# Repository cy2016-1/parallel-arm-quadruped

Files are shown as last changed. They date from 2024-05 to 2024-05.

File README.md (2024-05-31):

# 并联臂四足

#### 硬件设计
    单片机：STM32F103C8T6
    电源方案：7.4V-12V输入，通过XL4005E1输出5V给舵机供电，再通过RT9013输出3.3V给单片机供电
    通信：NRF24L01
    舵机驱动：方案一：直接通过2个定时器产生8路PWM输出；方案二：通过IIC与PCA9685通信，驱动舵机
#### 软件架构
1.产生摆线方程，生成足端轨迹规划
    sigma=2pi(t-t_T)/(faaiTs);
    Xep=((xf-xs)(sigma-(sin(sigma))))/(2pi)+xs;
    Zep=h(1-cos(sigma))/2;

2.运动学逆解（余弦定理、勾股定理）
输入图片说明 屏幕截图
A、B分别为两个舵机输出轴心，它们相距距离为2a。足端坐标（x,y）由轨迹规划而来。L1，L2为腿部的上臂和下臂臂长。
θ1和θ2才是我们需要求解的舵机转动角度。
而θ1=90°-（β-γ），所以求解顺序为：L3→β→γ

3.用MPU6050传感器反馈数据来实现姿态控制
输入图片说明 屏幕截图

#### 注意事项

1.  组装舵机前，先下载舵机回中位的程序，即将 main.c中的这部分注释掉，如图
输入图片说明 屏幕截图
2.  注意舵机引脚分配：FR-前→A6，FR-后→A7;BR-前→B0,BR-后→B1;BL-前→B8,BL-后→B9;FL-前→B6,FL-后→B7

#### 展示
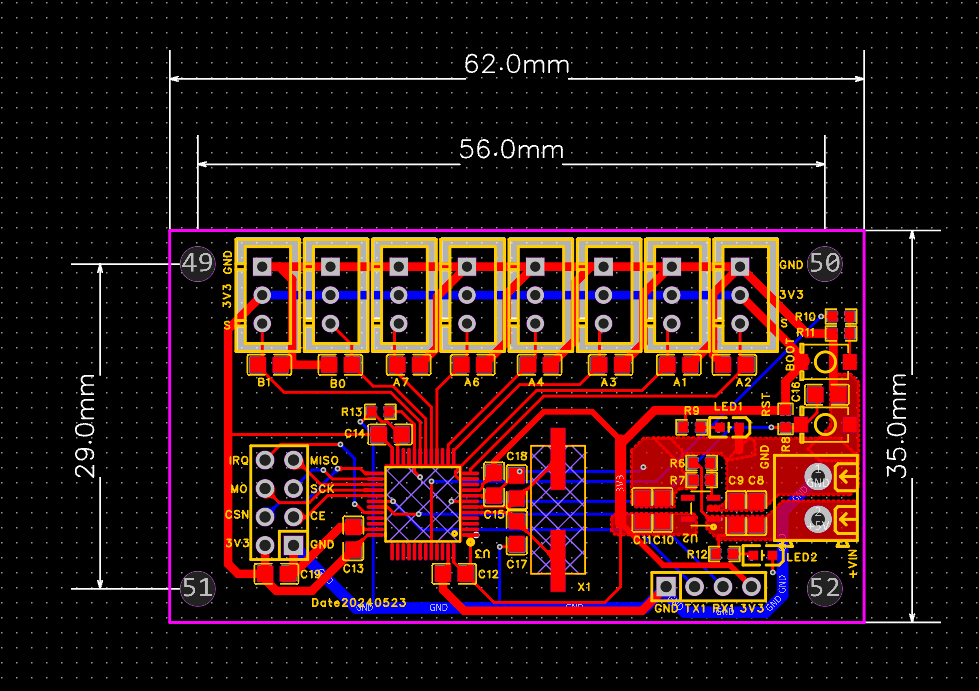
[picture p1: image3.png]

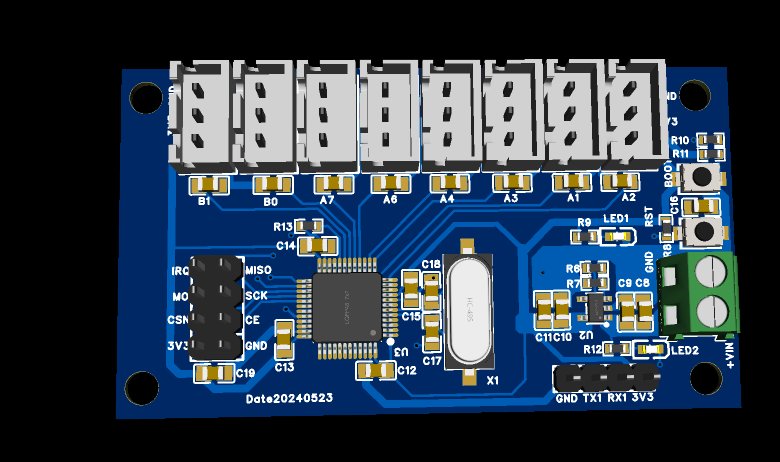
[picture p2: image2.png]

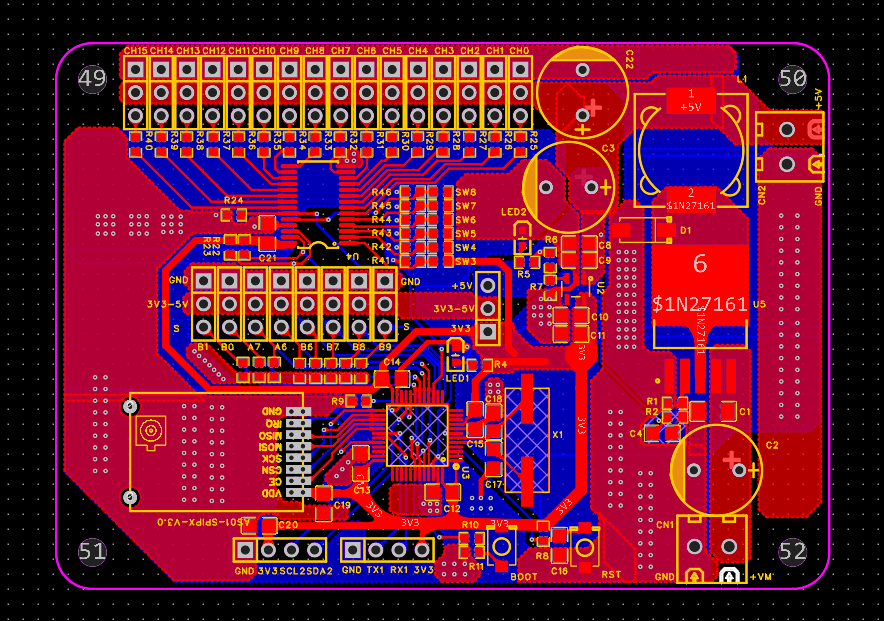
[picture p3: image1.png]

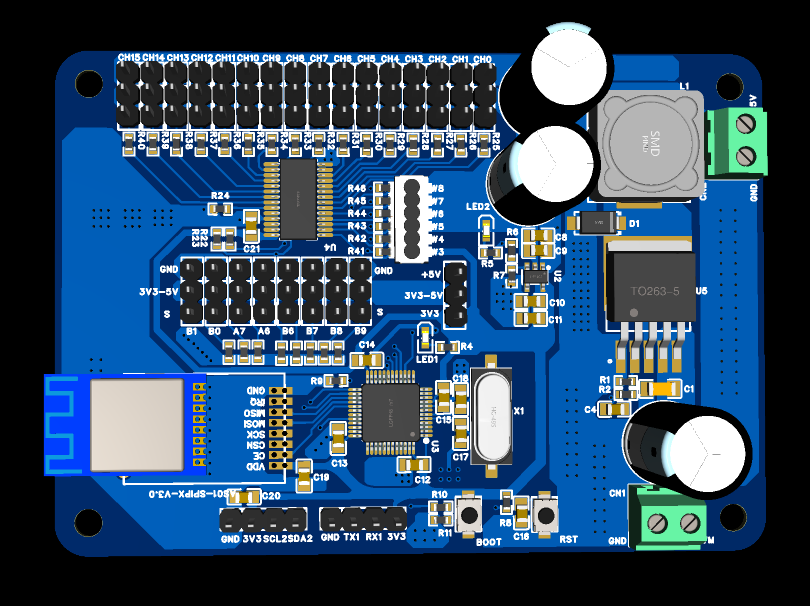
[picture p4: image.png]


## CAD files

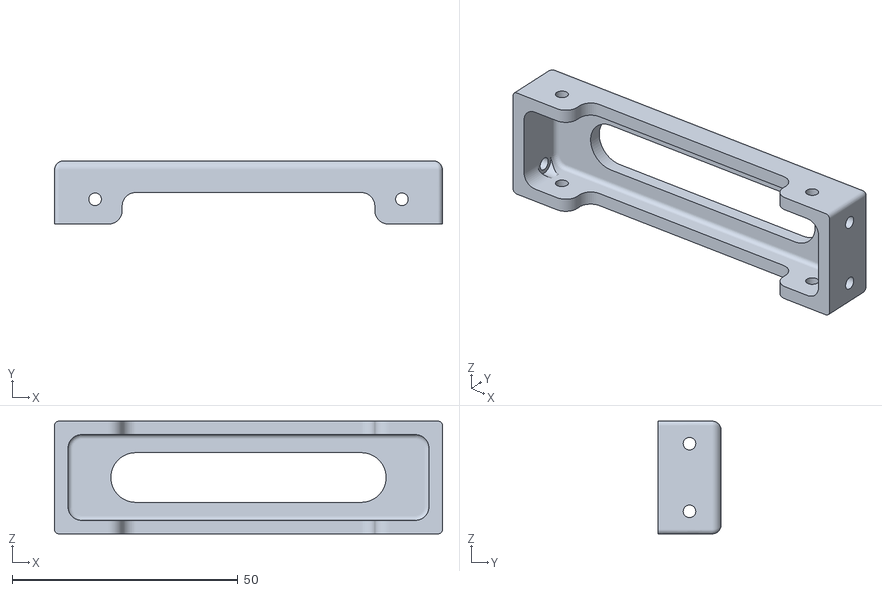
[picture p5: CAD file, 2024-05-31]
STL文件/前后横板.stl
86.0 x 14.0 x 25.0

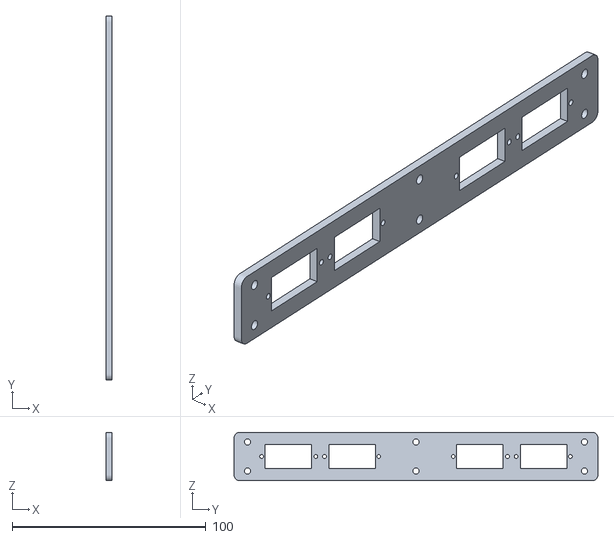
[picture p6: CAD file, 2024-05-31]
STL文件/舵机固定板.stl
3.00 x 188.0 x 25.0

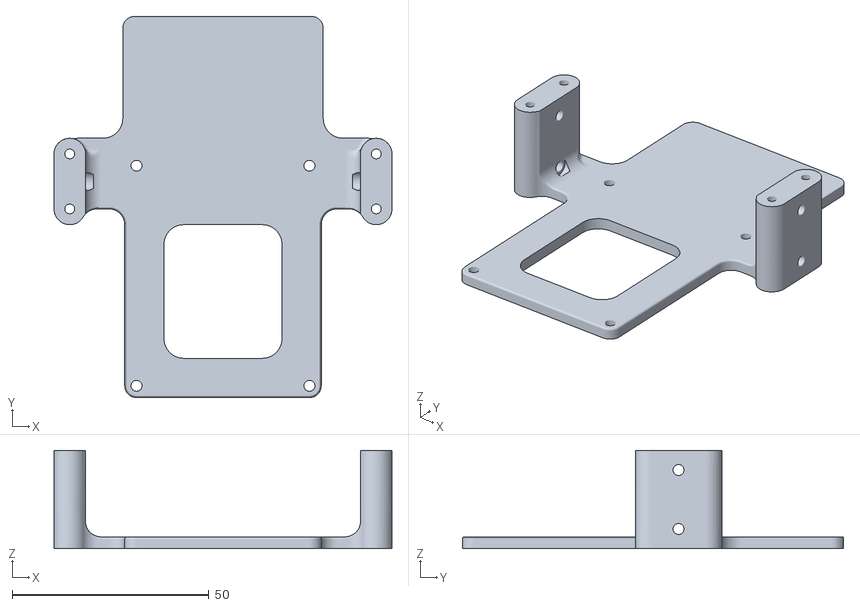
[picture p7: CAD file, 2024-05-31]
STL文件/中间横板.stl
86.0 x 97.0 x 25.0

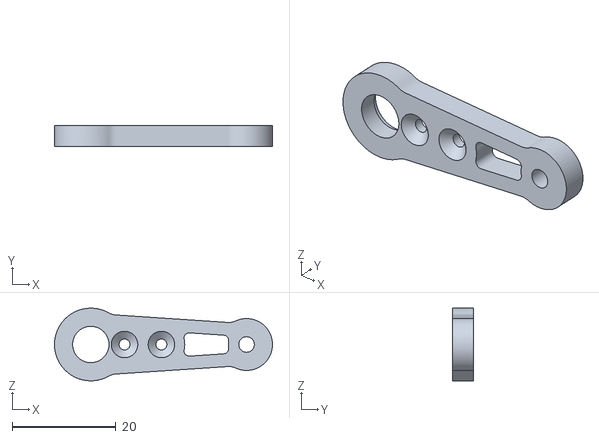
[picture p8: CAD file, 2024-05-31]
STL文件/大臂.stl
42.0 x 4.00 x 14.0

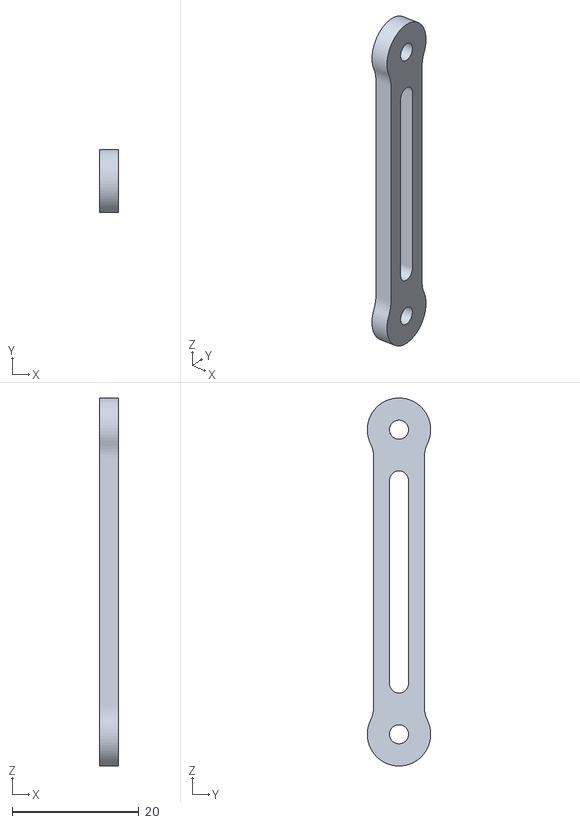
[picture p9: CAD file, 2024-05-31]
STL文件/下臂后.stl
3.00 x 9.99 x 58.0

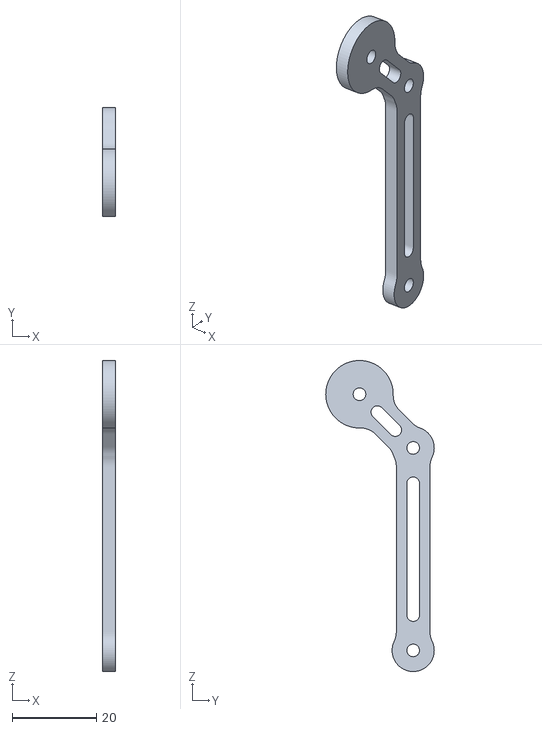
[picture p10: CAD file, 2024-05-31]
STL文件/下臂前.stl
3.00 x 25.7 x 73.7

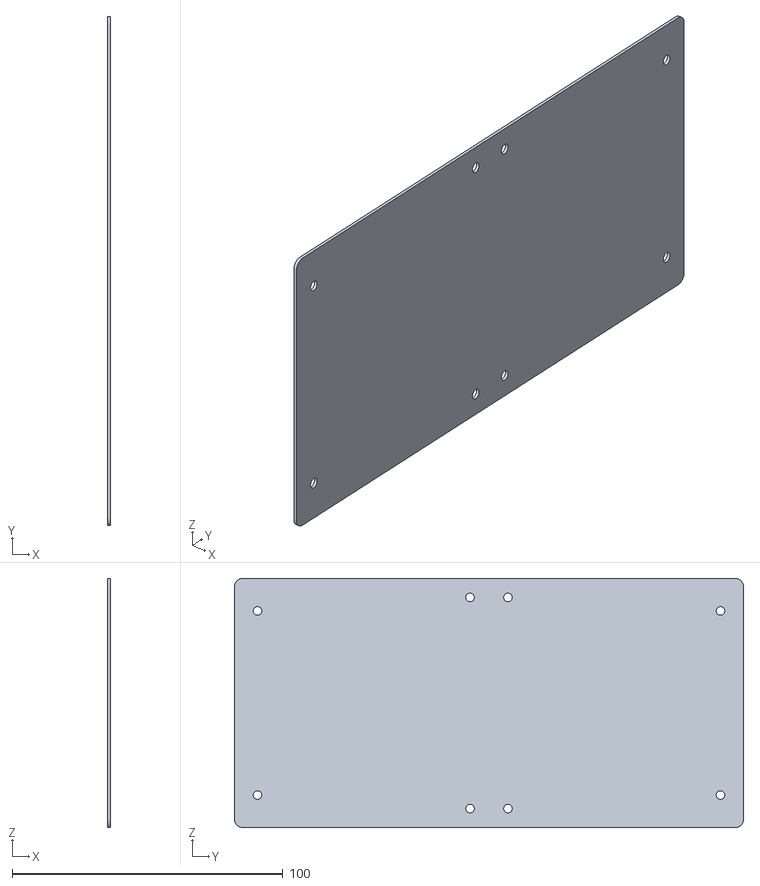
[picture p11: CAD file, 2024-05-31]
STL文件/机身上下盖板.stl
1.00 x 188.0 x 92.0

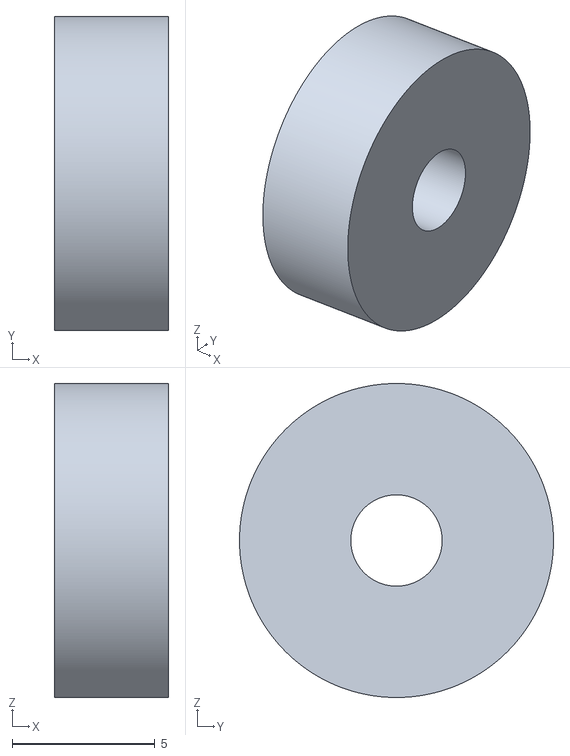
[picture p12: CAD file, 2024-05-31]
STL文件/圆垫3mm.stl
4.00 x 11.0 x 11.0

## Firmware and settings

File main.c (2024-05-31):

#include "./SYSTEM/sys/sys.h"
#include "./SYSTEM/usart/usart.h"
#include "./SYSTEM/delay/delay.h"
#include "./BSP/TIMER/gtim.h"

#include "./BSP/NRF24L01/nrf24L01.h"
  
#include "./BSP/KEY/key.h"
#include "demo.h"
//#include "./BSP/PCA9685/pca9685.h"
//#include "./BSP/IIC/myiic.h"

#include <math.h>

extern TIM_HandleTypeDef g_tim3_pwm_ch_handle;     /* 定时器3ch3句柄     PB0     */
extern TIM_HandleTypeDef g_tim2_pwm_ch_handle;     /* 定时器3ch3句柄     PB0     */
extern TIM_HandleTypeDef g_tim4_pwm_ch_handle;     /* 定时器3ch3句柄     PB0     */

extern float imu_buf[10];
extern float walk_xy[8],t_speed;
extern int Motion_state;
int16_t map(float val,int16_t map_I_min,int16_t map_I_max,int16_t map_O_min,int16_t map_O_max)
{
	int16_t map_val=(int16_t)(val);
  if(map_val<map_I_min)
    {
      return map_O_min;
    }
  if(map_val>map_I_max)
    {
      return map_O_max; 	
    }
//		return  (map_val*(map_O_max-map_O_min)/(map_I_max-map_I_min))+(map_O_max-map_O_min)/2;
  return  (map_val*10/9)+150;
}
float L1=30,L2=48,L3=62.0474,DIS_X=21/2;	
float P_x=0,P_y=60,P_z=60;					


float Xs=0,Xf=10,H=10,PI=3.14,delta_X=0;//Xf=-20

float x1,x2,x3,x4,y1,y2,y3,y4;
extern float pi;
float ABl_x,ABl_z,AB2_x,AB2_z,AB3_x,AB3_z,AB4_x,AB4_z;
float pwm_out[4][4]={{0,150,0,150},{0,150,0,150},{0,150,0,150},{0,150,0,150}};
void IK_calculate(float IK_x,float IK_y,int IK_i){
	float IK_angle1,IK_angle2,IK_angle3,IK_angle4,IK_angle5,IK_x_1,IK_y_1,IK_angle6,IK_angle7,IK_angle8,IK_angle9=0.3336;
	if((IK_x-DIS_X)==0){
		IK_angle1=0;
	}else{
		IK_angle1=asin((IK_x-DIS_X)/(sqrt((IK_x-DIS_X)*(IK_x-DIS_X)+IK_y*IK_y)));
	}
	IK_angle2=acos(((IK_x-DIS_X)*(IK_x-DIS_X)+IK_y*IK_y+L1*L1-L3*L3)/(2*L1*sqrt((IK_x-DIS_X)*(IK_x-DIS_X)+IK_y*IK_y)));
	IK_angle3=1.57-IK_angle2-IK_angle1;
	pwm_out[IK_i][2]=-IK_angle3;
	pwm_out[IK_i][3]=map(-IK_angle3*57.3,-90,90,50,250);
	IK_angle4=acos((L1*L1+L3*L3-((IK_x-DIS_X)*(IK_x-DIS_X)+IK_y*IK_y))/(2*L1*L3));
	IK_angle5=IK_angle4-IK_angle3-IK_angle9;
	IK_x_1=L1*cos(IK_angle3)-L2*cos(IK_angle5)+DIS_X*2;
	IK_y_1=L1*sin(IK_angle3)+L2*sin(IK_angle5);
	
	if(IK_x_1==0){
		IK_angle6=0;
	}else{
		IK_angle6=asin(IK_x_1/(sqrt(IK_x_1*IK_x_1+IK_y_1*IK_y_1)));
	}
	IK_angle7=acos((IK_x_1*IK_x_1+IK_y_1*IK_y_1+L1*L1-L2*L2)/(2*L1*sqrt(IK_x_1*IK_x_1+IK_y_1*IK_y_1)));
	IK_angle8=1.57-IK_angle7+IK_angle6;
	pwm_out[IK_i][0]=IK_angle8;
	pwm_out[IK_i][1]=map(IK_angle8*57.3,-90,90,50,250);
}

void PWM_OUT(){
	__HAL_TIM_SET_COMPARE(&g_tim3_pwm_ch_handle, GTIM_TIM3_PWM_CH1, 300-pwm_out[0][1]);
	__HAL_TIM_SET_COMPARE(&g_tim3_pwm_ch_handle, GTIM_TIM3_PWM_CH2, 300-pwm_out[0][3]);

	__HAL_TIM_SET_COMPARE(&g_tim3_pwm_ch_handle, GTIM_TIM3_PWM_CH3, 300-pwm_out[1][1]);
	__HAL_TIM_SET_COMPARE(&g_tim3_pwm_ch_handle, GTIM_TIM3_PWM_CH4, 300-pwm_out[1][3]);
	
	__HAL_TIM_SET_COMPARE(&g_tim4_pwm_ch_handle, GTIM_TIM4_PWM_CH3, pwm_out[2][1]);
	__HAL_TIM_SET_COMPARE(&g_tim4_pwm_ch_handle, GTIM_TIM4_PWM_CH4, pwm_out[2][3]);
	
	__HAL_TIM_SET_COMPARE(&g_tim4_pwm_ch_handle, GTIM_TIM4_PWM_CH1, pwm_out[3][1]);
	__HAL_TIM_SET_COMPARE(&g_tim4_pwm_ch_handle, GTIM_TIM4_PWM_CH2, pwm_out[3][3]);
		
}


void cal_ges(float PIT,float ROL,float l,float b,float w){
	float YA=0,P,R,Y;
	
//	P=PIT;
//	R=ROL;
//	Y=YA;
	P=PIT*pi/180;
	R=ROL*pi/180;
	Y=YA*pi/180;

	ABl_x=l/2 - (l*cos(P)*cos(Y))/2 + (b*cos(P)*sin(Y))/2;
//	ABl_y=w/2 - (b*(cos(R)*cos(Y) + sin(P)*sin(R)*sin(Y)))/2 - (l*(cos(R)*sin(Y) - cos(Y)*sin(P)*sin(R)))/2;
	ABl_z= - (b*(cos(Y)*sin(R) - cos(R)*sin(P)*sin(Y)))/2 - (l*(sin(R)*sin(Y) + cos(R)*cos(Y)*sin(P)))/2;

	AB2_x=l/2 - (l*cos(P)*cos(Y))/2 - (b*cos(P)*sin(Y))/2;
//	AB2_y=(b*(cos(R)*cos(Y) + sin(P)*sin(R)*sin(Y)))/2 - w/2 - (l*(cos(R)*sin(Y) - cos(Y)*sin(P)*sin(R)))/2;
	AB2_z=(b*(cos(Y)*sin(R) - cos(R)*sin(P)*sin(Y)))/2 - (l*(sin(R)*sin(Y) + cos(R)*cos(Y)*sin(P)))/2;

	AB3_x=(l*cos(P)*cos(Y))/2 - l/2 + (b*cos(P)*sin(Y))/2;
//	AB3_y=w/2 - (b*(cos(R)*cos(Y) + sin(P)*sin(R)*sin(Y)))/2 + (l*(cos(R)*sin(Y) - cos(Y)*sin(P)*sin(R)))/2;
	AB3_z=(l*(sin(R)*sin(Y) + cos(R)*cos(Y)*sin(P)))/2 - (b*(cos(Y)*sin(R) - cos(R)*sin(P)*sin(Y)))/2;

	AB4_x=(l*cos(P)*cos(Y))/2 - l/2 - (b*cos(P)*sin(Y))/2;
//	AB4_y=(b*(cos(R)*cos(Y) + sin(P)*sin(R)*sin(Y)))/2 - w/2 + (l*(cos(R)*sin(Y) - cos(Y)*sin(P)*sin(R)))/2;
	AB4_z=(b*(cos(Y)*sin(R) - cos(R)*sin(P)*sin(Y)))/2 + (l*(sin(R)*sin(Y) + cos(R)*cos(Y)*sin(P)))/2;
}
int len,dir_state=0;
int change_state=1;

float trim_x[4]={0,0,0,0},raise_val=0,raise_val_max=35;
float trim_h[4]={12,3,4,2};
uint8_t main_tmp_buf[32],main_t;
uint16_t IS[4];
extern int turn;
extern int fb_state;
int main(void)
{
	
  HAL_Init();                             /* 初始化HAL库 */
  sys_stm32_clock_init(RCC_PLL_MUL9);     /* 设置时钟, 72Mhz */
  delay_init(72);                         /* 延时初始化 */
  usart_init(9600);                     /* 串口初始化为115200 */
 
  gtim_tim3_pwm_ch_init(2000 - 1, 720 - 1);/* 1Mhz的计数频率,2Khz的PWM. */
	gtim_tim4_pwm_ch_init(2000 - 1, 720 - 1);/* 1Mhz的计数频率,2Khz的PWM. */
  btim_timx_int_init(2000 - 1, 360 - 1);
  atim_timx_int_init(2000 - 1, 360 - 1);

	demo_run();  
			
//	PCA_Servo_Init(50,90);

  NRF24L01_SPI_Init();    		//初始化NRF24L01

  while(NRF24L01_Check())
    {
      printf("硬件查寻不到NRF24L01无线模块\n");

      HAL_Delay(1000);
    }
  printf("NRF24L01无线模块硬件连接正常\n");

  NRF24L01_RX_Mode();

  printf("进入数据接收模式\n");

  while (1)
    {
			if(NRF24L01_RxPacket(main_tmp_buf)==0)
				{
					for(main_t=0; main_t<4; main_t++)
						{
							IS[main_t] = (uint16_t) (main_tmp_buf[2*main_t] << 8) | main_tmp_buf[2*main_t+1];
						}
				}
			t_speed=(float)IS[0]/4096*0.09+0.01;
			if(t_speed>0.1){
					t_speed=0.1;
				}else if(t_speed<0.01){
					t_speed=0.01;
				}
			if(IS[3]<1800){
				turn=1;
			}else if(IS[3]>2400){
				turn=2;
			}else{
				turn=0;
			}
			if(IS[2]<1800){
				fb_state=2;
			}else if(IS[2]>2400) {
				fb_state=1;
			}else{
				fb_state=0;
			}
			delta_X=Xf-Xs;
			raise_val=(float)IS[1]/4096*2*raise_val_max-raise_val_max;
			if(main_tmp_buf[9]){
					Motion_state=1;
					delta_X=2*(Xf-Xs);
			}else{
				Motion_state=2;
				delta_X=Xf-Xs;
			}
			x1=delta_X*walk_xy[0]+Xs-10;
			y1=H*walk_xy[1];
			x2=delta_X*walk_xy[2]+Xs+10;
			y2=H*walk_xy[3];
			x3=delta_X*walk_xy[4]+Xs+10;
			y3=H*walk_xy[5];
			x4=delta_X*walk_xy[6]+Xs-10;
			y4=H*walk_xy[7];
			cal_ges(imu_buf[1]+raise_val,imu_buf[0],119,92,116.4);
			IK_calculate(x1+trim_x[0]+AB2_x,y1+trim_h[0]+P_y+AB2_z,0);  //FR
			IK_calculate(x2+trim_x[1]+AB4_x,y2+trim_h[1]+P_y+AB4_z,1);	//BR
			IK_calculate(x3+trim_x[2]+AB3_x,y3+trim_h[2]+P_y+AB3_z,2);	//BL
			IK_calculate(x4+trim_x[3]+ABl_x,y4+trim_h[3]+P_y+ABl_z,3);	//FR
			PWM_OUT();
			
    }
}


//			if (g_usart_rx_sta & 0x8000)        /* 接收到了数据? */
//			{
//					int i=1,point_state=0,point_index=1;
//					float M_rx_val=0;
//					char get_t,M_get_index;
//					len = g_usart_rx_sta & 0x3fff;  /* 得到此次接收到的数据长度 */
//					get_t=(char)g_usart_rx_buf[0];
//					M_get_index=get_t;
//					for(i=1;i<len;i++){
//							get_t=(char)g_usart_rx_buf[i];
//							if(get_t=='.'){
//									point_state=1;
//									point_index=1;
//							}
//							if(point_state&&get_t>=48&&get_t<=57){
//									point_index*=10;
//									M_rx_val+=(float)(get_t-'0')/point_index;
//									if(point_index==100){
//											break;
//									}
//							}else if(get_t>=48&&get_t<=57){
//									M_rx_val=M_rx_val*10+(get_t-'0');
//							}
//					}
//					switch(M_get_index){
//						case 'Q':
//									if((char)g_usart_rx_buf[1]=='-'){
//											dir_state=1;
//											Xf=0-M_rx_val;
//											}else{
//													dir_state=0;
//													Xf=M_rx_val;
//									}
//									break;
//						case 'W':
//									if((char)g_usart_rx_buf[1]=='-'){
//											dir_state=1;
//											H=0-M_rx_val;
//											}else{
//													dir_state=0;
//													H=M_rx_val;
//									}
//									break;
//								case 'v':
//									if((char)g_usart_rx_buf[1]=='-'){
//											dir_state=1;
//											trim_h[0]=0-M_rx_val;
//											}else{
//													dir_state=0;
//													trim_h[0]=M_rx_val;
//									}
//									break;
//								case 'b':
//									if((char)g_usart_rx_buf[1]=='-'){
//											dir_state=1;
//											trim_h[1]=0-M_rx_val;
//											}else{
//													dir_state=0;
//													trim_h[1]=M_rx_val;
//									}
//									break;
//								case 'n':
//									if((char)g_usart_rx_buf[1]=='-'){
//											dir_state=1;
//											trim_h[2]=0-M_rx_val;
//											}else{
//													dir_state=0;
//													trim_h[2]=M_rx_val;
//									}
//									break;
//								case 'm':
//									if((char)g_usart_rx_buf[1]=='-'){
//											dir_state=1;
//											trim_h[3]=0-M_rx_val;
//											}else{
//													dir_state=0;
//													trim_h[3]=M_rx_val;
//									}
//									break;
//							case 'P':
//									if(M_rx_val==1){
//										Motion_state=1;fb_state=2;turn=0;
//									}else if(M_rx_val==2){
//										Motion_state=1;fb_state=0;turn=0;
//									}
//									break;
//							case 'O':
//									if((char)g_usart_rx_buf[1]=='-'){
//											dir_state=1;
//											change_state=0-M_rx_val;
//											}else{
//													dir_state=0;
//													change_state=M_rx_val;
//									}
//									break;
//					}
//					g_usart_rx_sta = 0;
//					i=1;point_state=0;point_index=1;M_get_index=' ';M_rx_val=0;
//			}

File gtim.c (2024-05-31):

#include "./BSP/TIMER/gtim.h"
#include "./SYSTEM/usart/usart.h"
#include "./BSP/NRF24L01/nrf24L01.h"
#include <math.h>
#include "demo.h"

#define POLEPAIRS 14
#define hall_Dir_0 4
#define hall_Dir_1 5
#define SPEEDMULT 600000

#define ADC_DMA_BUF_SIZE        50 * 2      /* ADC DMA采集 BUF大小, 应等于ADC通道数的整数倍 */
uint16_t g_adc_dma_buf[ADC_DMA_BUF_SIZE];   /* ADC DMA BUF */

extern uint8_t g_adc_dma_sta;               /* DMA传输状态标志, 0,未完成; 1, 已完成 */

/*********************************以下是通用定时器PWM输出实验程序*************************************/

TIM_HandleTypeDef g_tim3_pwm_ch_handle;     /* 定时器x句柄 */

TIM_HandleTypeDef g_tim4_pwm_ch_handle;     /* 定时器x句柄 */

TIM_HandleTypeDef a_timx_handle; /* 定时器x句柄 */

TIM_HandleTypeDef b_timx_handle; /* 定时器x句柄 */


/**
 * @brief       通用定时器TIMX 通道Y PWM输出 初始化函数（使用PWM模式1）
 * @note
 *              通用定时器的时钟来自APB1,当PPRE1 ≥ 2分频的时候
 *              通用定时器的时钟为APB1时钟的2倍, 而APB1为36M, 所以定时器时钟 = 72Mhz
 *              定时器溢出时间计算方法: Tout = ((arr + 1) * (psc + 1)) / Ft us.
 *              Ft=定时器工作频率,单位:Mhz
 *
 * @param       arr: 自动重装值。
 * @param       psc: 时钟预分频数
 * @retval      无
 */
void gtim_tim3_pwm_ch_init(uint16_t arr, uint16_t psc)
{
  TIM_OC_InitTypeDef tim3_oc_pwm_chy  = {0};                          /* 定时器PWM输出配置 */

  g_tim3_pwm_ch_handle.Instance = GTIM_TIM3_PWM;                     /* 定时器x */
  g_tim3_pwm_ch_handle.Init.Prescaler = psc;                         /* 定时器分频 */
  g_tim3_pwm_ch_handle.Init.CounterMode = TIM_COUNTERMODE_UP;        /* 递增计数模式 */
  g_tim3_pwm_ch_handle.Init.Period = arr;                            /* 自动重装载值 */
  HAL_TIM_PWM_Init(&g_tim3_pwm_ch_handle);                           /* 初始化PWM */

  tim3_oc_pwm_chy.OCMode = TIM_OCMODE_PWM1;                           /* 模式选择PWM1 */
  tim3_oc_pwm_chy.Pulse = arr / 2;                                    /* 设置比较值,此值用来确定占空比 */
  /* 默认比较值为自动重装载值的一半,即占空比为50% */
  tim3_oc_pwm_chy.OCPolarity = TIM_OCPOLARITY_HIGH;                    /* 输出比较极性为低 */

  HAL_TIM_PWM_ConfigChannel(&g_tim3_pwm_ch_handle, &tim3_oc_pwm_chy, GTIM_TIM3_PWM_CH1); /* 配置TIMx通道y */
  HAL_TIM_PWM_Start(&g_tim3_pwm_ch_handle, GTIM_TIM3_PWM_CH1);       /* 开启对应PWM通道 */

  HAL_TIM_PWM_ConfigChannel(&g_tim3_pwm_ch_handle, &tim3_oc_pwm_chy, GTIM_TIM3_PWM_CH2); /* 配置TIMx通道y */
  HAL_TIM_PWM_Start(&g_tim3_pwm_ch_handle, GTIM_TIM3_PWM_CH2);       /* 开启对应PWM通道 */
	
  HAL_TIM_PWM_ConfigChannel(&g_tim3_pwm_ch_handle, &tim3_oc_pwm_chy, GTIM_TIM3_PWM_CH3); /* 配置TIMx通道y */
  HAL_TIM_PWM_Start(&g_tim3_pwm_ch_handle, GTIM_TIM3_PWM_CH3);       /* 开启对应PWM通道 */

  HAL_TIM_PWM_ConfigChannel(&g_tim3_pwm_ch_handle, &tim3_oc_pwm_chy, GTIM_TIM3_PWM_CH4); /* 配置TIMx通道y */
  HAL_TIM_PWM_Start(&g_tim3_pwm_ch_handle, GTIM_TIM3_PWM_CH4);       /* 开启对应PWM通道 */
}


void gtim_tim4_pwm_ch_init(uint16_t arr, uint16_t psc)
{
  TIM_OC_InitTypeDef tim4_oc_pwm_chy  = {0};                          /* 定时器PWM输出配置 */

  g_tim4_pwm_ch_handle.Instance = GTIM_TIM4_PWM;                     /* 定时器x */
  g_tim4_pwm_ch_handle.Init.Prescaler = psc;                         /* 定时器分频 */
  g_tim4_pwm_ch_handle.Init.CounterMode = TIM_COUNTERMODE_UP;        /* 递增计数模式 */
  g_tim4_pwm_ch_handle.Init.Period = arr;                            /* 自动重装载值 */
  HAL_TIM_PWM_Init(&g_tim4_pwm_ch_handle);                           /* 初始化PWM */

  tim4_oc_pwm_chy.OCMode = TIM_OCMODE_PWM1;                           /* 模式选择PWM1 */
  tim4_oc_pwm_chy.Pulse = arr / 2;                                    /* 设置比较值,此值用来确定占空比 */
  /* 默认比较值为自动重装载值的一半,即占空比为50% */
  tim4_oc_pwm_chy.OCPolarity = TIM_OCPOLARITY_HIGH;                    /* 输出比较极性为低 */

  HAL_TIM_PWM_ConfigChannel(&g_tim4_pwm_ch_handle, &tim4_oc_pwm_chy, GTIM_TIM4_PWM_CH1); /* 配置TIMx通道y */
  HAL_TIM_PWM_Start(&g_tim4_pwm_ch_handle, GTIM_TIM4_PWM_CH1);       /* 开启对应PWM通道 */

  HAL_TIM_PWM_ConfigChannel(&g_tim4_pwm_ch_handle, &tim4_oc_pwm_chy, GTIM_TIM4_PWM_CH2); /* 配置TIMx通道y */
  HAL_TIM_PWM_Start(&g_tim4_pwm_ch_handle, GTIM_TIM4_PWM_CH2);       /* 开启对应PWM通道 */
	
  HAL_TIM_PWM_ConfigChannel(&g_tim4_pwm_ch_handle, &tim4_oc_pwm_chy, GTIM_TIM4_PWM_CH3); /* 配置TIMx通道y */
  HAL_TIM_PWM_Start(&g_tim4_pwm_ch_handle, GTIM_TIM4_PWM_CH3);       /* 开启对应PWM通道 */

  HAL_TIM_PWM_ConfigChannel(&g_tim4_pwm_ch_handle, &tim4_oc_pwm_chy, GTIM_TIM4_PWM_CH4); /* 配置TIMx通道y */
  HAL_TIM_PWM_Start(&g_tim4_pwm_ch_handle, GTIM_TIM4_PWM_CH4);       /* 开启对应PWM通道 */
}
/**
 * @brief       定时器底层驱动，时钟使能，引脚配置
                此函数会被HAL_TIM_PWM_Init()调用
 * @param       htim:定时器句柄
 * @retval      无
 */
void HAL_TIM_PWM_MspInit(TIM_HandleTypeDef *htim)
{
  if (htim->Instance == GTIM_TIM3_PWM)
    {
      GPIO_InitTypeDef gpio_init_struct;
      GTIM_TIM3_PWM_CH_GPIO_CLK_ENABLE();               /* 开启通道y的CPIO时钟 */
      GTIM_TIM3_PWM_CH_CLK_ENABLE();
//        GTIM_TIM3_PWM_CH1_GPIO_REMAP();

      gpio_init_struct.Pin = GTIM_TIM3_PWM_CH1_GPIO_PIN; /* 通道y的CPIO口 */
      gpio_init_struct.Mode = GPIO_MODE_AF_PP;           /* 复用推完输出 */
      gpio_init_struct.Pull = GPIO_PULLDOWN;               /* 上拉 */
      gpio_init_struct.Speed = GPIO_SPEED_FREQ_HIGH;     /* 高速 */
      HAL_GPIO_Init(GTIM_TIM3_PWM_CH1_GPIO_PORT, &gpio_init_struct);
			
			gpio_init_struct.Pin = GTIM_TIM3_PWM_CH2_GPIO_PIN; /* 通道y的CPIO口 */
      gpio_init_struct.Mode = GPIO_MODE_AF_PP;           /* 复用推完输出 */
      gpio_init_struct.Pull = GPIO_PULLDOWN;               /* 上拉 */
      gpio_init_struct.Speed = GPIO_SPEED_FREQ_HIGH;     /* 高速 */
      HAL_GPIO_Init(GTIM_TIM3_PWM_CH2_GPIO_PORT, &gpio_init_struct);

      gpio_init_struct.Pin = GTIM_TIM3_PWM_CH3_GPIO_PIN; /* 通道y的CPIO口 */
      gpio_init_struct.Mode = GPIO_MODE_AF_PP;           /* 复用推完输出 */
      gpio_init_struct.Pull = GPIO_PULLDOWN;               /* 上拉 */
      gpio_init_struct.Speed = GPIO_SPEED_FREQ_HIGH;     /* 高速 */
      HAL_GPIO_Init(GTIM_TIM3_PWM_CH3_GPIO_PORT, &gpio_init_struct);

      gpio_init_struct.Pin = GTIM_TIM3_PWM_CH4_GPIO_PIN; /* 通道y的CPIO口 */
      gpio_init_struct.Mode = GPIO_MODE_AF_PP;           /* 复用推完输出 */
      gpio_init_struct.Pull = GPIO_PULLDOWN;               /* 上拉 */
      gpio_init_struct.Speed = GPIO_SPEED_FREQ_HIGH;     /* 高速 */
      HAL_GPIO_Init(GTIM_TIM3_PWM_CH4_GPIO_PORT, &gpio_init_struct);
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

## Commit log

2024-05-31 新建 程序
2024-05-31 add 程序.
2024-05-31 删除文件 程序/robotdog0531
2024-05-31 主要程序
2024-05-31 删除文件 程序
2024-05-31 基于stm32f103c8t6的舵机驱动程序
2024-05-31 基于stm32f103c8t6的遥控器发送端程序
2024-05-31 遥控器发射端控制板和四足舵机驱动电路板→用立创EDA打开查阅
2024-05-31 add STL文件.
2024-05-31 删除文件 STL文件
2024-05-31 新建 STL文件
2024-05-31 3D打印文件
    [下臂前.stl, 下臂后.stl, 中间横板.stl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]
